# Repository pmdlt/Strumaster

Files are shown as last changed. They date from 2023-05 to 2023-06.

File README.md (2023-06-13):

# Strumaster project

> EPFL ***Making intelligent things*** (**CS-358**) semester project
> 
> Introducing Strumaster, the connected & automated guitar that combines
> art, technology, and entertainment in a unique and innovative way.
> With its industrial-chic design and whimsical features, Strumaster is
> not just a guitar, it's a blend of form and function.



## Project Description
### Goal
The ultimate goal of the Strumaster project is a guitar that can play itself, providing a MIDI file via a web app. It also has of course the function to play a note by itself, and has a whole host of debugging functions (manage engine by engine, string by string, etc.).

## List of supplies
- 1x Guitar
- 1x Wooden plateform (120x70x5 cm)
- 1x Arduino Uno
- 1x ESP8266
- 1x 12V power supply
- 1x 9V power supply
- 1x Adafruit PCA9685
- 2x CNC shield
- 6x stepper motor driver
- 6x stepper motor
- 6x stepper motor timing Belt Pulley
- 100cm of timing belt
- 6x servo
- 10x 6Mx65 screw
- 16x 6M nuts
- 30x 3Mx10 screw
- 12x 3mx5 screw
- a lot of wires
- zip-ties

## List of Parts to 3d print

### Servo Part:
- 6x servoStrum
- 1x servoPlateformLeft
- 1x servoPlateformCenter
- 1x servoPlateformRight
- 2x servoPlateformBottom

### Stepper Part:
- 1x plateformSteppers
- 2x plateformGuider
- 6x neckGuiderUniversalTop
- 6x neckGuiderUniversalBottom
- 1x neckGuiderFret2Top
- 1x neckGuiderFret2Bottom
- 1x neckGuiderFret0Top
- 1x neckGuiderFret0Bottom

### Others:
- 3x supportCNC_Shield
- 1x supportPCA9685
- 5x guitarHolder
- 10x cableGuider

## List of Parts laser cut in plexiglas 
- 6x rails

# ESP
The ESP serves as a master, it is the brain of our system. It creates a WiFi which the user has to connect to and it handles all requests asked by the user. The requests are then transmitted to the Adafruit PCA or to the Arduino board in terms of orders to the servos or the steppers, respectively. In order to play a song, a csv file is sent to the ESP which build 6 queues of notes and their timings, one for each string. It then dequeues the notes one by one, places the stepper at its correct fret, and activate the servo when note must be played.

# Servos
In this project the servos are used to pluck the strings. They are positioned were the fingers usually pluck the strings, and act as replacement for the musician's ones. For this, we had to design and print a bridge on top of the guitar to hold them, as well as code a library to play different notes. 

### Hardware
For the hardware, we use Adafruit PCA9685 and six 6v servos. The bridge on the guitar that hold the servos are comprised of 3 different parts: one servoPlateformLeft, one servoPlateformRight and tzo servoPlateformBottom which serves respectivly as holders and legs for holding the servoPlateformCenter on top of the guitar cords, which in turn hold the servos. Those parts are made to assemble with one another to form a single bridge which holds each servo above a cord. It should be noted that the servos are not positioned on top of the guitar hole, but rather a little more downstram of the cords. This design choice was made to mitigate the impact that pushing down on the string had on the sound made by plucking it with the servos. The final printed parts were the six servoStrum, which were attached to the servos and were the parts touching the string. To construct these parts, we printed them, and glued a small sheet of soft plastic (packaging plastic PET) of 10 mm x 5 mm in between the legs of that 3d printed part. This was done because 3d printed parts are not soft enough to produce a quality sound when plucking the guitar, and since we need to adjust the length of that plastic sheet it was easier to have it separated.

The rest of the hardware include electronics. For this, we connected the servos to the adafruit board and the adafruit board to a 5v output from the arduino, and connected the signal controls and ground to the ESP8266. This allowed us to control the servos from the esp using the adafruit library.

### Software (Arduino/ESP part)
The software part consisted in creating the library for using the servos (servo_library.h and servo_library.ino) and using them in the server file (server.ino). The coding of this part was pretty straightforward: we first setup the function to a 45 degree angle above the cords and then the function playSingleCord could be used to activate servos. Other functions of the library include moving several servos over specific cords, as well as moving servos to specific angles. The angle value of the servos always oscillate between 45 and 135 degrees, and is stored in memory by the program.

### Software (Client part)


To control the guitar, a modern web-app based on [VueJS](https://vuejs.org/)/[Vuetify](https://vuetifyjs.com/en/) and hosted on [Netlify](https://www.netlify.com/) was created. It send POST and GET request to the ESP, witch is on the same WiFi.

# Steppers and Rails
In order to do the fretting, we use rails that constantly push the strings. They are moved to the correct fret using stepper motors.

The steppers are controlled by the Arduino board, with two CNC shields between them to serves as drivers. We made a simple labrary that allow the steppers to take steps in a non-blocking way (one stepper must not wait for the other to have finish its travel) and without loss of speed when several steppers are actuated at the same time. This was necessary for the guitar, as the rails can move at the same time in a music.
We also coded a Serial protocol of communication to get orders from the ESP. It was very straightforward, the ESP communication an integer corresponding to an order along a value, which can be an string id, a number of steps or a fret id. To move to a specific fret on the guitar, we counted the number of steps needed from the 1st fret to reach the desired fret.
We also made a simple dictionnary to map a note id, which goes from 0 to 60, to a string and a fret. We made this because of the small RAM constraints and to make communications as small as possible. Indeed, the ESP just has to communicate a small integer, instead of a string id and a number of steps.

### Necessary measurements

When you are starting the build, it is important to note that even though all guitars are standardized in terms of length (4/4, 3/4, 1/2, 1/4), the neck sizes may vary.
For example, in the case of 4/4 guitars, the neck widths (measured at the top) vary between 43 and 45 mm for acoustic, 51 and 55mm for classical and 41 and 45 mm for electric. In our case it is a 4/4 classic with a neck width of 52mm. The design we chose, requires the rails to run in parallel in order to not intersect, for this reason it is wise to first verify the maximum number of frets you can work with. How you can do this:

 1. Choose a rail width such that you have at least 2mm between each pair of rails   						
 (you need this for stability reasons and in order for the guiding gate entrances to be larger than the exits which assures fluent rail movement) [less than 4mm is never recommended]
 
 2. After you have chosen your rail width, you need to find the optimal position such that you can act on a sufficient set of strings. I. E., as each string has a different angle you need to find how many frets of each string can be covered when it is intersected with a rail going perpendicullarly to the nut (white part before the first fret). The minimum is your constraint, it should be at least 8 frets to have enough variety.
 3. When you have your fret coverage, you need to measure its length - the distance between the nut and your furthest fret.
 4. You can then use this distance to set the distance of the stepper platform from the nut. It is determined by two reference points - the axis of the steppers that are going to be closest to the guitar and the nut. This distance should be equal to the fret coverage + 1-2 cm of headroom. We need to do this because your timing belt length is the same as your fret coverage (again + the headroom) and it needs to be able to fit its entire length in that space when you are trying to play your furthest fret. The belt cannot pass through the 3d part on the nut as it is the one that holds the rails the tightest.

## Other Hardware

### Guitar Holders and Plank
In order to fix all our hardware and guitar together, we used a 120x70x5 cm wooden epicea plank to put bellow the guitar, as well as % 3d small printed pieces used to keep the guitar from moving from its spot on the plank. Those holders where positioned at the bottem, beginning of neck and sides of the guitar, and screwed on the metal plank.

## Electric scheme:

Guitar-1

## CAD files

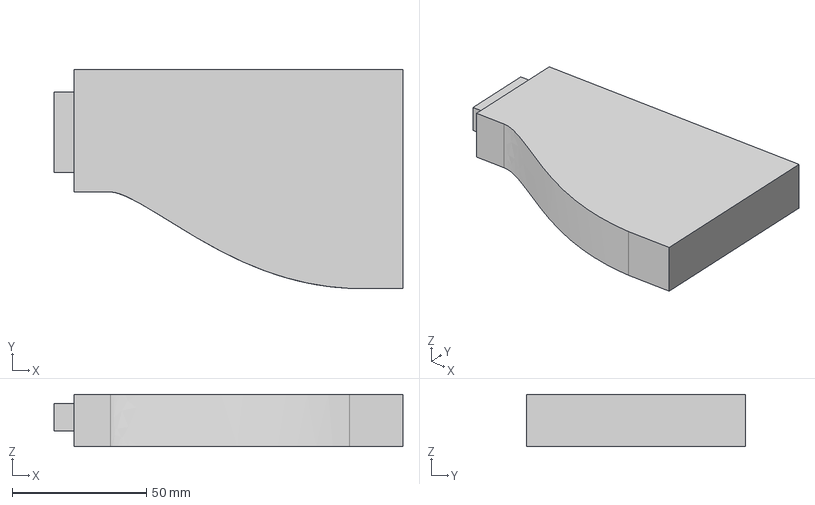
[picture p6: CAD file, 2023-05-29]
partsToPrint/servoPart/servoPlateformRight.step
130.0 x 81.5 x 19.5 mm

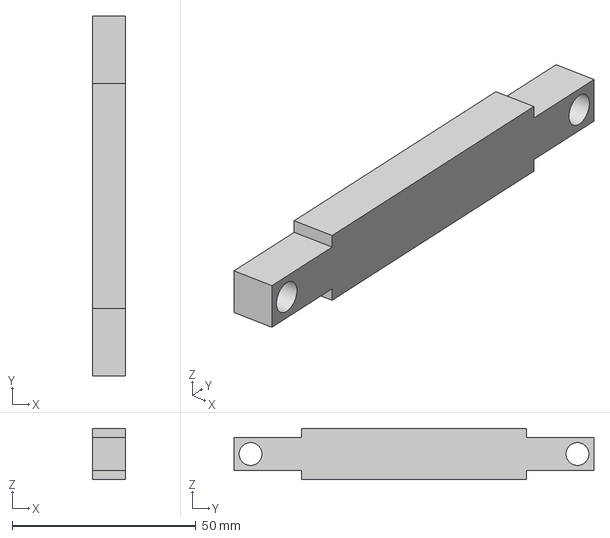
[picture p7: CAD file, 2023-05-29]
partsToPrint/stepperPart/neckGuiderUniversalBottom.step
9.00 x 97.9 x 14.0 mm

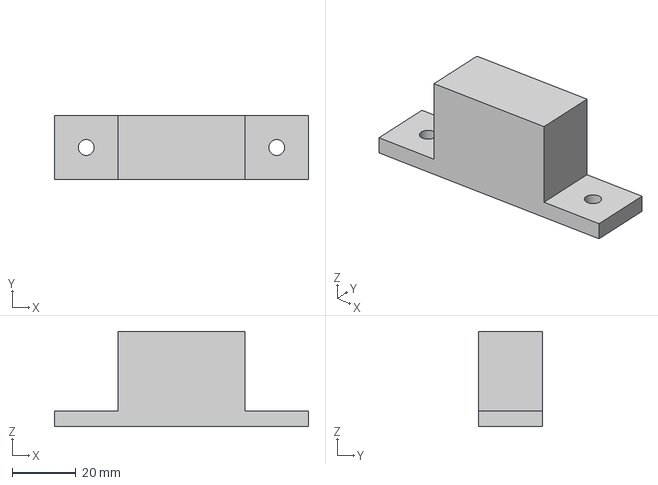
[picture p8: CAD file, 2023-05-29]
partsToPrint/others/guitarHolder.step
80.0 x 20.0 x 30.0 mm

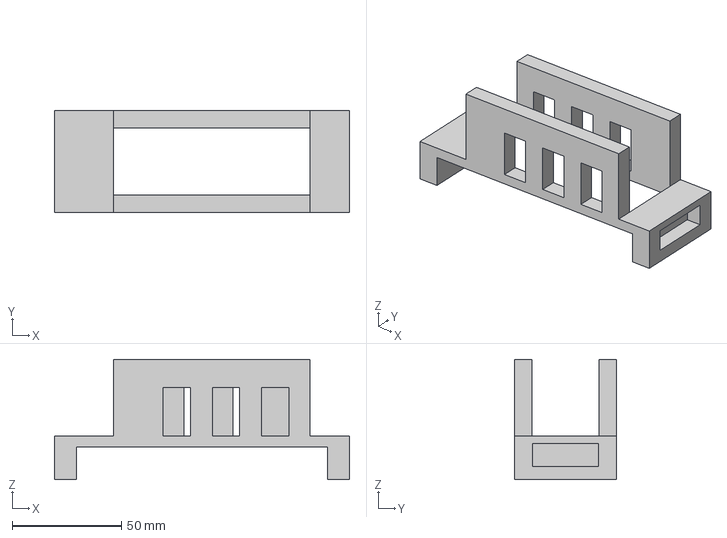
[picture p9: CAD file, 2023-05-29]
partsToPrint/servoPart/servoPlateformCenter.step
135.0 x 46.5 x 55.0 mm

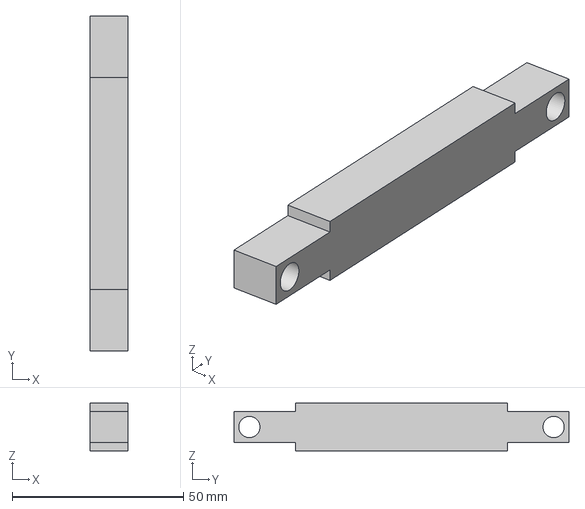
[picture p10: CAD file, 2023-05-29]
partsToPrint/stepperPart/neckGuiderFret2Bottom.step
11.0 x 97.9 x 14.0 mm

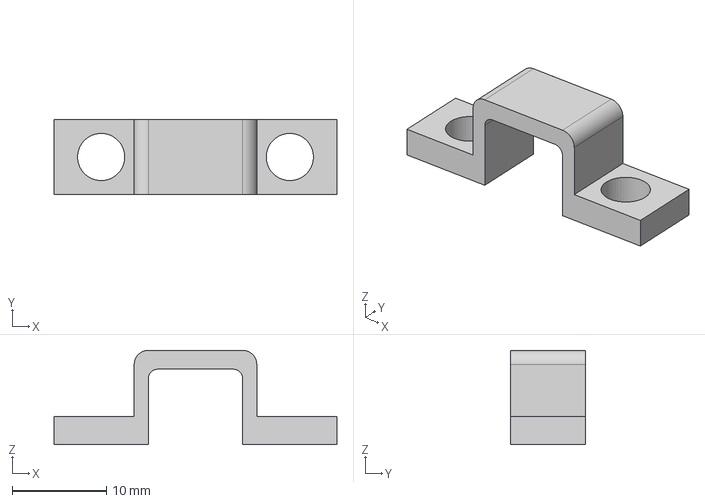
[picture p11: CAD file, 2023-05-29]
partsToPrint/others/cableGuider.step
30.0 x 8.00 x 10.0 mm

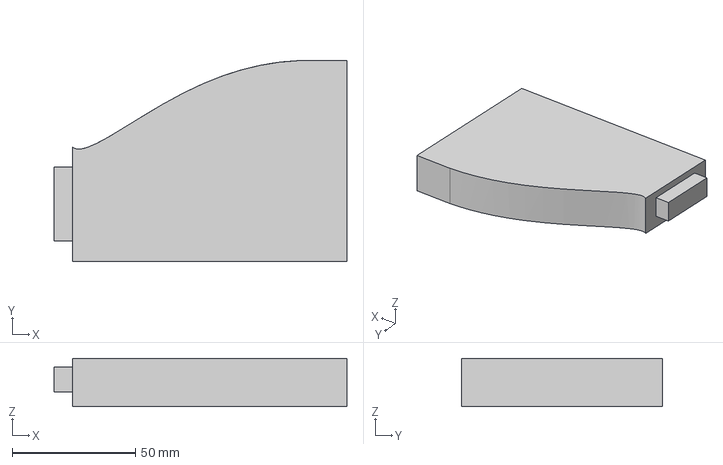
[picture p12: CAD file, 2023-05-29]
partsToPrint/servoPart/servoPlateformLeft.step
119.0 x 81.5 x 19.5 mm

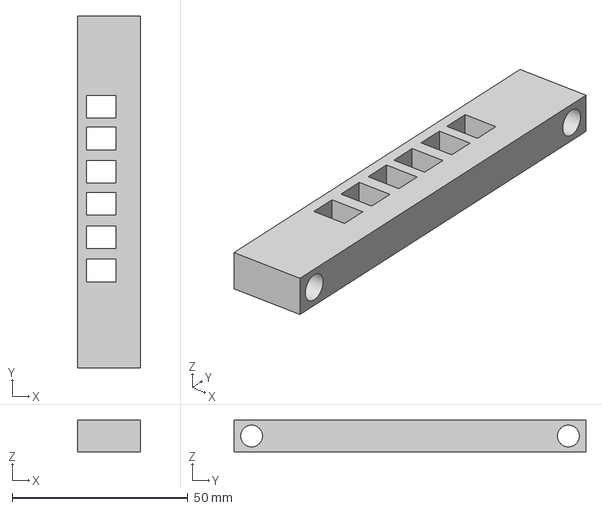
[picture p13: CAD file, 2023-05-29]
partsToPrint/stepperPart/NeckGuiderFret0Top.step
18.0 x 100.0 x 9.00 mm

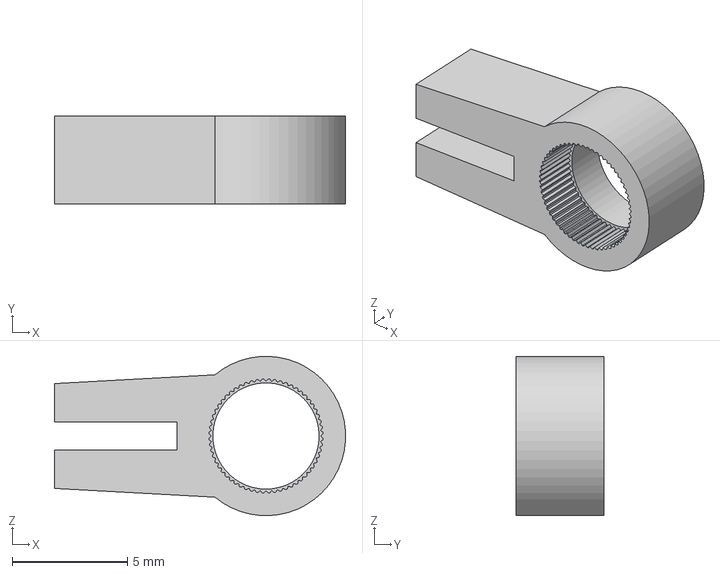
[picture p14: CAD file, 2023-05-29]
partsToPrint/servoPart/servoStrum.step
12.6 x 3.80 x 6.89 mm

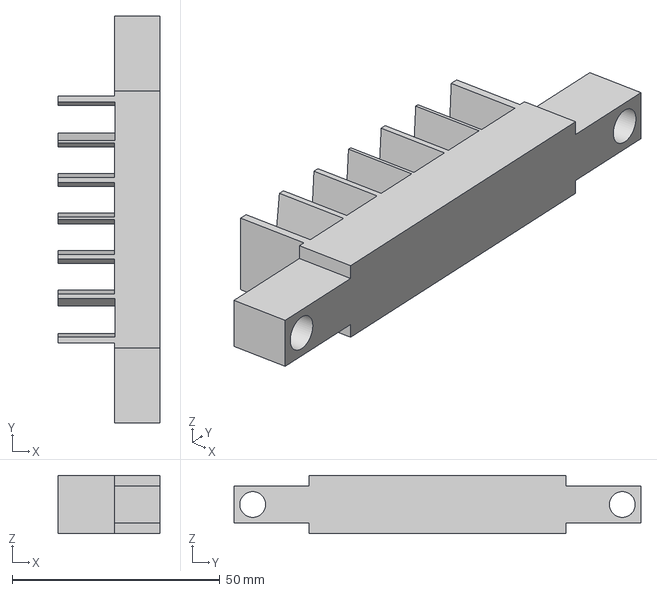
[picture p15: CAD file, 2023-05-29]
partsToPrint/stepperPart/neckGuiderFret2Top.step
24.6 x 97.9 x 14.0 mm

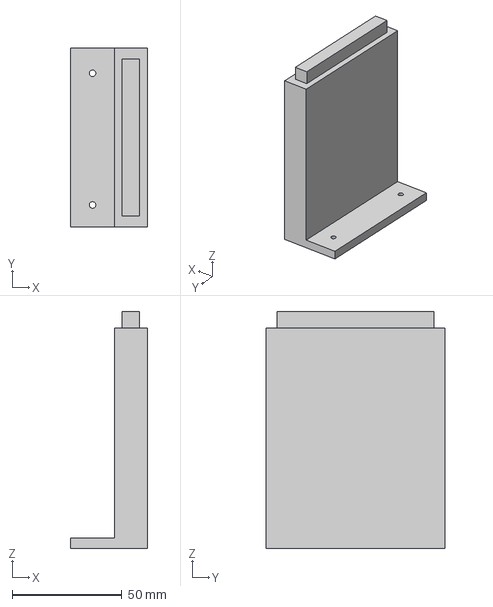
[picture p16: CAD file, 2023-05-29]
partsToPrint/servoPart/servoPlateformBottom.step
35.0 x 81.5 x 108.0 mm

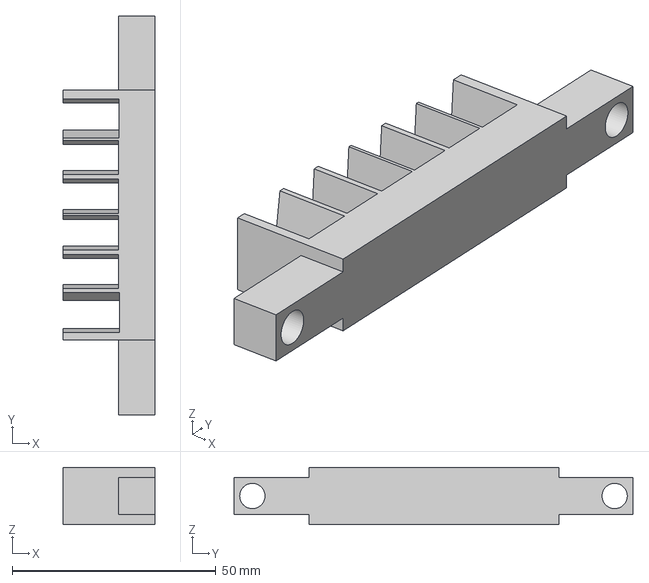
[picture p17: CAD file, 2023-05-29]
partsToPrint/stepperPart/neckGuiderUniversalTop.step
22.6 x 97.9 x 14.0 mm

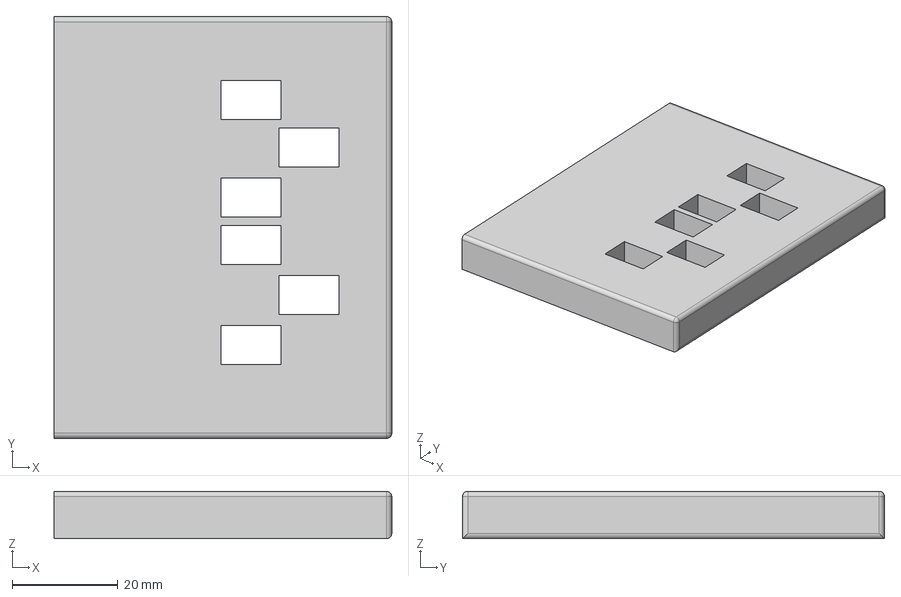
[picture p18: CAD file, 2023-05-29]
partsToPrint/stepperPart/guiderPlateform.step
64.0 x 80.0 x 9.00 mm

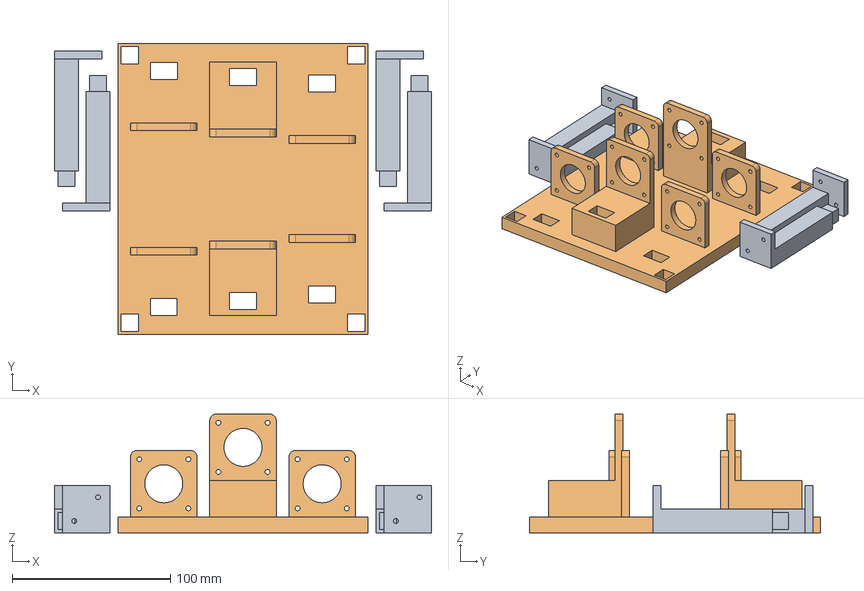
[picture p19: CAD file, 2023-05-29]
partsToPrint/stepperPart/platformSteppers.step
238.0 x 184.0 x 75.0 mm

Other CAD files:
partsToPrint/others/supportCNC_Shield.step
partsToPrint/others/supportPCA9685.step
partsToPrint/stepperPart/neckGuiderFret0Bottom.step

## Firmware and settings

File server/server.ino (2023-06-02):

#include <ESP8266WiFi.h>
#include <ESP8266WebServer.h>
#include <AccelStepper.h>
#include <Wire.h>
#include <SoftwareSerial.h>

#include "servo_library.h"

// Webserver config
const char* ssid = "strumaster_control";
const char* password = "12345678";
IPAddress local_ip(192, 168, 174, 140);
IPAddress gateway(192, 168, 1, 1);
IPAddress subnet(255, 255, 255, 0);
ESP8266WebServer server(80);


// Program variables
bool connected = 0;
bool is_playing = false;
uint8_t nbFrets = 10;  // number of frets handled by strings

// CNC shield handling
#define DEFAULT_CNC_TIME_LET 3000
int cnc_pin = D4;
unsigned long cnc_timer = 0;

void setup() {
  Serial.begin(9600);

  // Servos init
  setupServos(10, 11, 12, 13, 14, 15);

  //cnc shield init
  pinMode(cnc_pin, OUTPUT);

  // WiFi initialisation
  WiFi.softAP(ssid, password);
  WiFi.softAPConfig(local_ip, gateway, subnet);
  delay(100);

  // Commands handle
  server.on("/connect", handleConnect);
  server.on("/stop", handleStop);
  server.on("/pause", handlePause);
  server.on("/resume", handleResume);
  server.on("/play_song", handlePlay);
  server.on("/reset_all", handleReset); 
  server.onNotFound(handleNotSupported);

  server.on("/load_song", HTTP_POST, []() {  // arg: POST_plain
    handleLoad();
  });
  server.on("/load_song", HTTP_OPTIONS, handleCORS);

  server.on("/play_note", HTTP_GET, []() {  // arg: id
    handlePlayNote();
  });

  server.on("/debug_stepper", HTTP_GET, []() {  // arg: function, id, value
    handleDebugStepper();
  });

  server.on("/debug_servo", HTTP_GET, []() {  // arg: id
    handleDebugServo();
  });

  server.enableCORS(true);
  server.begin();  
  
}
void loop() {
  // server
  server.handleClient();
  
  // Playing a song
  if (is_playing) loopTiming();

  // Cnc handling
  if (is_playing || millis() < cnc_timer) {
    digitalWrite(cnc_pin, LOW);
  } else {
    digitalWrite(cnc_pin, HIGH);
  }
}

//----------------- debug functions

void activate_stepper(int id_note) {
  cnc_timer = millis() + DEFAULT_CNC_TIME_LET;
  Serial.printf("%d,\n", id_note);
}

void debug_stepper(int id_stepper, int steps) {
  cnc_timer = millis() + DEFAULT_CNC_TIME_LET;
  Serial.printf("%d,%d,\n", id_stepper, steps);
}

void trigger_stepper(int id_stepper) {
  cnc_timer = millis() + 1000; // one second is enough
  debug_stepper(id_stepper, 10);
  delay(100);
  debug_stepper(id_stepper, -10);
}

void reverse_stepper(int id_stepper) {
  Serial.printf("%d,%d,\n", -1, id_stepper);
}

void reset_stepper(int id_stepper) {
  cnc_timer = millis() + DEFAULT_CNC_TIME_LET;
  Serial.printf("%d,%d,\n", -4, id_stepper);
}

void calibrate_stepper(int id_stepper){
  Serial.printf("%d,%d,\n", -2, id_stepper);
}

void activate_servo(int id_servo) {
  playSingleCord(id_servo);
}



//----------------- request handling functions 

void handleConnect() {
  server.send(200, "text/plain", "Connexion successful. Try to play a note !");
}

void handlePause() {
  is_playing = false;
  server.send(200, "text/plain", "Song paused");
}

void handleResume() {
  is_playing = true;
  server.send(200, "text/plain", "Song resumed");
}

void handlePlay() {
  is_playing = true;
  startPlaying();
  server.send(200, "text/plain", "Song started ! Enjoy !");
}

void handleStop() {
  is_playing = false;
  resetQueues();
  server.send(200, "text/plain", "All motor off");
}

void handleReset() {
  cnc_timer = millis() + DEFAULT_CNC_TIME_LET;
  Serial.println("-5,");
  server.send(200, "text/plain", "Device reinitialized");
}

void handleNotSupported() {
  server.send(501, "text/plain", "Command not supported");
}

void handleLoad() {
    cnc_timer = millis() + DEFAULT_CNC_TIME_LET;
    setupTimings(server.arg("plain").c_str());
    is_playing = false;
    server.send(200, "text/plain", "Song was sent to the guitar. File was correctly loaded !");
}

void handlePlayNote() {
  int id = server.arg("id").toInt();
  digitalWrite(cnc_pin, LOW);
  activate_stepper(id);
  delay(DEFAULT_CNC_TIME_LET);
  activate_servo(id / nbFrets);

  server.send(200, "text/plain", "Note sent and played");
}

void handleDebugStepper() {
  int id = server.arg("id").toInt();
  int value = server.arg("value").toInt();
  String function = server.arg("function");
  int rtnv = 0;

  if        (function == "PlayNote") {
    rtnv = 1;
  } else if (function == "Steps") {
    rtnv = 2;
  } else if (function == "Reset") {
    rtnv = 3;
  } else if (function == "Reverse") {
    rtnv = 4;
  } else if (function == "Trigger") {
    rtnv = 5; //todo
  } else if (function == "Calibrate"){
    rtnv = 6; //todo
  } else if (function == "CalibrateAll"){
    rtnv = 7; //todo
  } else {
    server.send(501, "text/plain", "Unknown debug function !");
    return;
  }

  switch (rtnv) {
    // Make a stepper go to a certain note
    case 1:
      activate_stepper(value);
      break;

    // Move the stepper <value> steps
    case 2:
      debug_stepper(id, value);
      break;

    // Reset the stepper's position
    case 3:
      reset_stepper(id);
      break;

    // Reverse the stepper
    case 4:
      reverse_stepper(id);
      break;

    // Trigger
    case 5:
      trigger_stepper(id);
      break;
    
    // calibrate
    case 6:
      calibrate_stepper(id);
      break;

    // calibrate all
    case 7:
      Serial.println("-3");
      break;

    default:
      return;
  }

  server.send(200, "text/plain", "Debug function received by ESP !");
}

void handleDebugServo() {
  int id = server.arg("id").toInt();

  //playSingleCord(id);
  activate_servo(id);

  server.send(200, "text/plain", "Servo moved.");
}

void handleCORS() {
  server.sendHeader("Access-Control-Allow-Origin", "*");
  server.sendHeader("Access-Control-Allow-Methods", "POST, GET, OPTIONS");
  server.sendHeader("Access-Control-Max-Age", "10000");
  server.sendHeader("Access-Control-Allow-Headers", "Content-Type");
  server.send(204);
}

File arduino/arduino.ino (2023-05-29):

#define uint unsigned int

#include "stepper_librairy.h"
#include <string.h>
#include <SoftwareSerial.h>

const int frets[9] = {0,220,420,610,790,960,1120,1275,1425};


typedef struct {
  uint8_t string; // stepper id
  uint16_t position; // position where the stepper must go
} Note;
uint8_t currNote = -1;

Note translater[60];
StepperDriver steppers[6] = {
  StepperDriverConstructor(2,   5,    false), 
  StepperDriverConstructor(3,   6,    false), 
  StepperDriverConstructor(4,   7,    true),
  StepperDriverConstructor(8,   11,   false),
  StepperDriverConstructor(9,   12,   true),
  StepperDriverConstructor(10,  13,   false)
  }; // Contains the stepper drivers
SoftwareSerial ESP(0, 1); 

uint8_t nbSteppers = 6;
//-------------

void setup() {
  //setup ESP communication
  ESP.begin(9600);
  Serial.begin(9600);

  // Steppers initialisation
  for (int i = 2; i < 14; i++){
    pinMode(i, OUTPUT);
  }
  steppersLibrairySetup(nbSteppers, 1000);

  // translater initialisation
  for (int id = 0; id < nbSteppers; id++){
    for (int fret = 0; fret < 10; fret++){
      translater[id*10 + fret] = {id, frets[fret]};
    }
  }
}

void loop() {
  // we get a note
  uint8_t tmp = listenToESP();
  if (tmp != -1) {
    currNote = tmp;
    Note translation = translater[currNote];
    setGoal(&steppers[translation.string], translation.position);
  }

  // Do a step for all steppers needing one
  updateSteppers(steppers);
}

//----------------- stepper debug function

void reverseStepper(uint8_t id){
  steppers[id].reversedDir = !steppers[id].reversedDir;
}

void calibrateStepper(uint8_t id){
  steppers[id].position = 0;
  steppers[id].goal = 0;
}

void calibrateAllSteppers(){
  for (int id = 0; id < nbSteppers; id++){
    calibrateStepper(id);
  }
}

void resetStepper(uint8_t id){
  steppers[id].goal = 0;
}

void resetAllSteppers(){
  for (int id = 0; id < nbSteppers; id++){
    resetStepper(id);
  }
}


/**
  Non-blocking function, which listen to the esp
  @return A note id (0-59) if the ESP has sent a new one, -1 otherwise. Call "doSteps" if ESP require a stepper to do a certain # of steps
*/
uint8_t listenToESP(){
  if (ESP.available()) { // Check if there's data available from the ESP8266
    String rawData = ESP.readStringUntil('\n');
                                                        Serial.println(rawData);
    int splittedData[3] = {0, 0, 0};
    size_t nbData = 0;
    uint index = 0;
    uint8_t tokenIndexes[2] = {0, 0};
    while(index < rawData.length()) {
      if (rawData.charAt(index) == ','){
        tokenIndexes[1] = index;
        splittedData[nbData] = rawData.substring(tokenIndexes[0], tokenIndexes[1]).toInt();
        tokenIndexes[0] = index + 1;
        nbData += 1;
      }
      index +=1;
    }
    if (nbData == 2) {
      //case reverse
      if (splittedData[0] == -1) {
        reverseStepper(splittedData[1]);
        return -1;
      } 
      
      // case calibrate
      if (splittedData[0] == -2) {
        calibrateStepper(splittedData[1]); 
        return -1;
      } 

      //case reset
      if (splittedData[0] == -4) {
        resetStepper(splittedData[1]); 
        return -1;
      }
      
      // case where we have to move the stepper 
      doSteps(&steppers[splittedData[0]], splittedData[1]); 
      return -1; 
    } else if (nbData == 1) {
      if (splittedData[0] == -3) {
        calibrateAllSteppers(); 
        return -1;
      }

      if (splittedData[0] == -5) {
        resetAllSteppers(); 
        return -1;
      }

      // case where we have to change the current note
      uint8_t note = splittedData[0];
      if (note>=0 && note<60) return note; // return the note
      Serial.println("Invalid note received from ESP");
    } else {
      Serial.println("Invalid data received from ESP");
    }  
  }
  return -1;
}

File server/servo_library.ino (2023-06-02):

#include <Adafruit_PWMServoDriver.h>

// called this way, it uses the default address 0x40
Adafruit_PWMServoDriver pwm = Adafruit_PWMServoDriver();
uint pin1_servo;
uint pin2_servo;
uint pin3_servo;
uint pin4_servo;
uint pin5_servo;
uint pin6_servo;
uint servo_array[6] = {MIN_ANGLE_PWM, MIN_ANGLE_PWM, MIN_ANGLE_PWM, MIN_ANGLE_PWM, MIN_ANGLE_PWM, MIN_ANGLE_PWM};

void setupServos(uint pin1, uint pin2, uint pin3, uint pin4, uint pin5, uint pin6) {
    // Adafruit PCA9685 initialisation
    pwm.begin();
    pwm.setPWMFreq(50);  // PWM frequency

    pin1_servo = pin1;
    pin2_servo = pin2;
    pin3_servo = pin3;
    pin4_servo = pin4;
    pin5_servo = pin5;
    pin6_servo = pin6;

    writeToAllServos(MIN_ANGLE_PWM);
    delay(1000);
    for (int i = 6; i >= 0; --i) {
      playSingleCord(i);
      delay(400);
    }
    
}

void playCords(int cord0, int cord1, int cord2, int cord3, int cord4, int cord5) {
  writeToServo(getPlayValue(0, cord0), getPlayValue(1, cord1), getPlayValue(2, cord2), getPlayValue(3, cord3), getPlayValue(4, cord4), getPlayValue(5, cord5));
}

int getPlayValue(int cord, int played) {
  if (played == 0) {
    return 0;
  }

  if (servo_array[cord] == MIN_ANGLE_PWM) {
    servo_array[cord] = MAX_ANGLE_PWM;
    return MAX_ANGLE_PWM;
  } else {
    servo_array[cord] = MIN_ANGLE_PWM;
    return MIN_ANGLE_PWM;
  }
}

void playSingleCord(int cord) {
  int cord_values[6] = {0, 0, 0, 0, 0, 0};
  cord_values[cord] = 1;

  playCords(cord_values[0], cord_values[1], cord_values[2], cord_values[3], cord_values[4], cord_values[5]);
}

void stopAll() {
  writeToAllServos(0);
}

void setAllToMiddle() {
  writeToAllServos((MAX_ANGLE_PWM - MIN_ANGLE_PWM) / 2);
}

void writeToServo(int value1, int value2, int value3, int value4, int value5, int value6) {
  if (value1) pwm.setPWM(pin1_servo, 0, value1);
  if (value2) pwm.setPWM(pin2_servo, 0, value2);
  if (value3) pwm.setPWM(pin3_servo, 0, value3);
  if (value4) pwm.setPWM(pin4_servo, 0, value4);
  if (value5) pwm.setPWM(pin5_servo, 0, value5);
  if (value6) pwm.setPWM(pin6_servo, 0, value6);
}

void writeToAllServos(int value) {
  for (int i = 0; i < 6; ++i) {
      servo_array[i] = value;
    }
  writeToServo(value, value, value, value, value, value);
}

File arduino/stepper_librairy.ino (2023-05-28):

uint NUM_STEPPERS = 0;
uint STEP_MICRODELAY = 0; //todo faire en sorte que l'interpas soit toujours le même, pour l'instant si y'en a 1 qui tourne il va super vite, si le 3 vont en même temps c'est plus lent 

void steppersLibrairySetup(uint nb, uint stepDelay){
  NUM_STEPPERS = nb;
  STEP_MICRODELAY = stepDelay;
}

// do a step for each stepper motor needing one.
void updateSteppers(StepperDriver steppers[]){
  // check that the librairy has been initialized
  if(NUM_STEPPERS != 0 && STEP_MICRODELAY != 0); else return;
  
  // Allow constant speed
  uint8_t nbActiveSteppers = 0;
  for (uint8_t i = 0; i < NUM_STEPPERS; ++i){
    if (steppers[i].goal - steppers[i].position) nbActiveSteppers += 1;
  }
  uint stepDelay = STEP_MICRODELAY / nbActiveSteppers;
  
  // Stepping
  for (uint8_t i = 0; i < NUM_STEPPERS; ++i){
    StepperDriver* stepper = &steppers[i];
    
    int diff = stepper->goal - stepper->position;
    if (diff == 0) continue;

    // Do the step in the right direction
    if (!((diff > 0) == stepper->reversedDir)) digitalWrite(stepper->dir, HIGH); else digitalWrite(stepper->dir, LOW); 
    digitalWrite(stepper->step, HIGH);
    delayMicroseconds(stepDelay);
    digitalWrite(stepper->step, LOW);
    stepper->position += diff > 0 ? 1 : -1;

    // small fix for heating
    digitalWrite(stepper->dir, LOW);
  }
}

StepperDriver StepperDriverConstructor(uint8_t stepPin, uint8_t dirPin, uint8_t isClockwise){
  StepperDriver stepper = {stepPin, dirPin, isClockwise, 0, 0};
  return stepper;
}

void setGoal(StepperDriver* stepper, int goal){
  stepper->goal = goal;
}

void doSteps(StepperDriver* stepper, int steps){
  stepper->goal = stepper->position + steps; 
}

void stopSteppers(StepperDriver steppers[]){
  for (uint i = 0; i < NUM_STEPPERS; ++i){
    steppers[i].goal = steppers[i].position;
  }
}

bool isRunning(StepperDriver* stepper, uint currTime){
  return currTime > stepper->blockedUntil;
}

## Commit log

2023-04-22 Add support multiple servo and steppers + debug stepper func
2023-04-22 Func debug servo + steppers ok !
2023-04-28 Made librairy for stepper controls using PCA9685
2023-05-03 Working for 2 steppers !
2023-05-04 Added Arduino code
2023-05-04 Removed Stepper references in server.ino
2023-05-05 Added debug functions in arduino
2023-05-06 Corrections after failed tests
    [arduino.ino, stepper_librairy.ino]
2023-05-06 Corrected bullshit Java code of Albert
    [arduino.ino]
2023-05-06 Optimisation de la complexité ( O(sqrt(n)) desormais)
2023-05-06 remove Serial.print
2023-05-06 added servo library
2023-05-09 Small fix for the button
2023-05-09 changed to non blocking servos
2023-05-14 changed servo library
2023-05-15 Change servo debug func
2023-05-16 Corrections to get the front end to work
    [server.ino]
2023-05-17 Connect button to func
2023-05-27 Arduino code to reset and reverse the steppers
    [arduino.ino]
2023-05-27 fix reset and revert
    [arduino.ino, server.ino]
2023-05-27 Small fixs for bug on server
    [server.ino]
2023-05-28 Attempt to fix not working reverse request
    [stepper_librairy.ino]
2023-05-29 Espace button
2023-05-29 Change button text
2023-05-29 Fixed Steppers going in wrong direction
    [arduino.ino]
2023-05-29 Fixed parkinson servo
2023-05-29 fixed bug which caused servos to be activated serveral times instead of 1
2023-05-29 Fixed bug causing wrong servo to activate on play_note
    [server.ino]
2023-05-29 Change nb of steppers
2023-05-29 add calibrate
2023-05-29 Style on button
2023-05-29 Add Calibrate & buttons for debug
2023-05-29 Change style of buttons
2023-05-29 Changed servos angles
2023-05-29 Fixed crash on attempting to play a midi file
    [server.ino]
2023-05-29 Add button for play Notes
2023-05-29 small servo fix
2023-05-29 Fix Reset not working
    [arduino.ino]
2023-05-29 start tuto
    [NeckGuiderFret0Top.step, cableGuider.step, guiderPlateform.step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]
2023-05-29 Try a fix to bugs on loading or playing midi file
    [server.ino, servo_library.ino]
2023-05-29 Fixed notes playing bug where servo had parkinson
2023-05-29 Upload sample MIDI files
2023-05-29 Update to new calibration protocols
2023-05-30 Fix ESP response on CalibrateAll
    [server.ino]
2023-05-30 Fix for the heating
    [server.ino]
2023-05-31 improve transform to only keep the track with the most notes and less shift
2023-05-31 lower angle servo
2023-05-31 refix angle servos
2023-05-31 Fix heating after a music
2023-05-31 speed up steppers
2023-05-31 2x speed on steppers
2023-06-01 rapport servo
2023-06-01 reset angle servo
2023-06-02 some more songs, spring is good, unbreak is hard
2023-06-02 Fixed major issue causing impossibility to strum
    [server.ino, servo_library.ino, song_playing.ino]
